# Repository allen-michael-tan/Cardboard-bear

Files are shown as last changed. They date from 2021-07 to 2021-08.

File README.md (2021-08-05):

# Cardboard bear

This repository showcases how a cardboard sculpture made by [Mr Bartholomew Ting](https://www.instagram.com/butterNmilk/) was modified and integrated with electronics to welcome students who step into Singapore Polytechnic's Makerspace. 

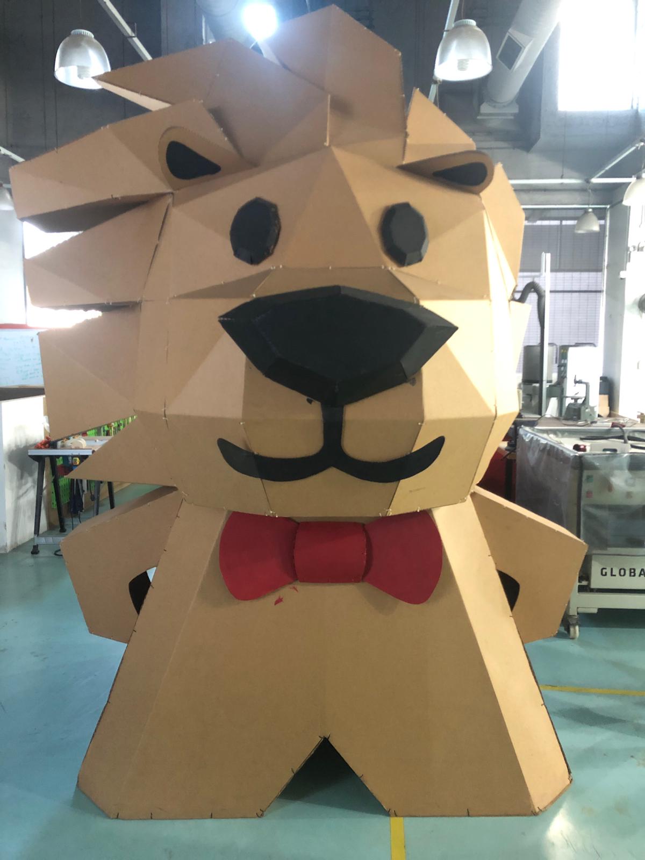
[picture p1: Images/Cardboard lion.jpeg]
Cardboard lion
 

This was how the original cardboard sculpture looked like. It was a lion, standing at a staggering height of over three meters! However, it was too tall to be placed in Makerspace which has a ceiling height of less than three meters. Therefore, modifications to the sculpture had to be made in order for it to be transported and placed in Makerspace.

Hence, the decision was made to remove the mane of the lion which happened to be enough height reduction for the sculpture to fit in Makerspace.

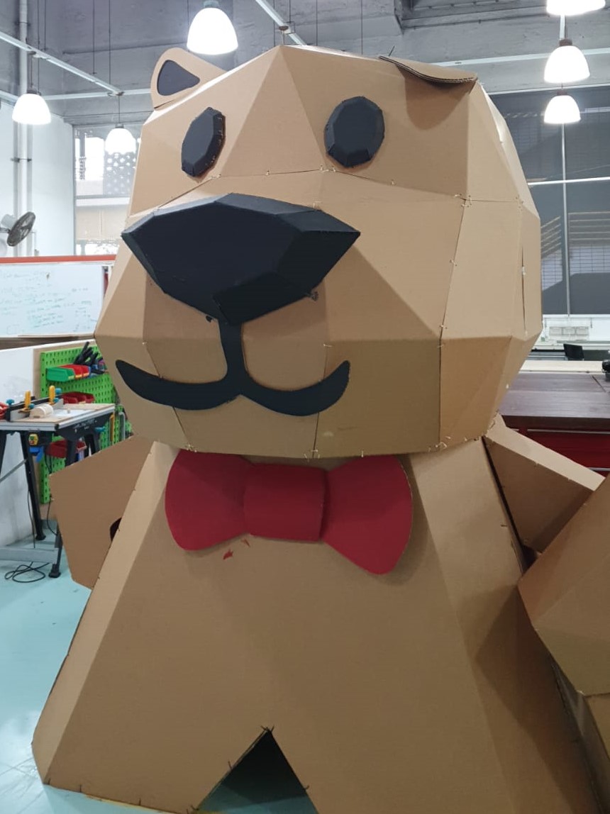
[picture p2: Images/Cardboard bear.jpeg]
Cardboard bear
 

This was how the cardboard sculpture after its "haircut". Without its mane, the lion looked very similar to a bear. Thus, the cardboard bear sculpture was born.

## Concept

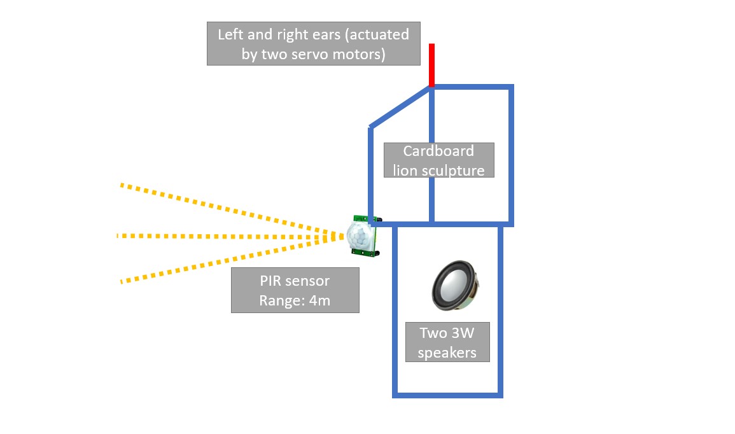
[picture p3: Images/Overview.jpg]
Overview


The concept of this project is when someone walks past the bear, it will be able to sense it through a sensor. After which, it will "interact" with the person by flapping its ear and playing a short audio track towards the person. 

Below is a short illustration of the concept.

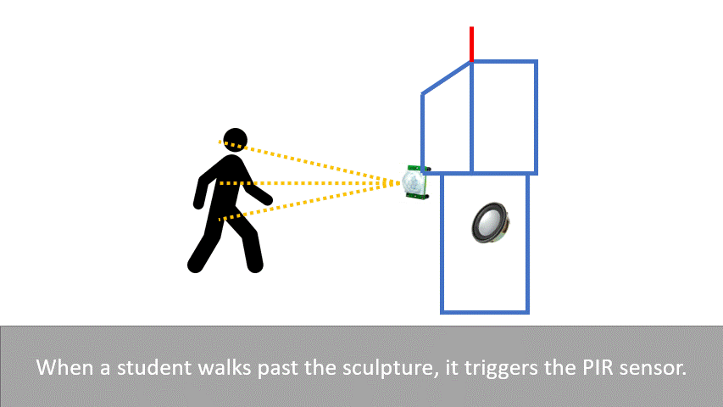
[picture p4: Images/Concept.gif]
Concept


## Design

All CAD models were modelled using Autodesk Inventor, the files can be found [here](https://github.com/allen-michael-tan/Kinematic-clock/tree/main/Inventor%20files).

The elctrical components used in this project are listed below. 

1. Arduino Uno [1]
2. SM-S3317B servo motors [2] 
2. PIR sensor [1]
3. DFR0299 MP3 player module [1] 
4. GF1002 amplifier module [1]
5. 3W speakers [2]
6. Button switch [1]
7. Blue LED bulb [1]
8. Red LED bulb [1]
9. 1k ohm resistor [3]

### Servo motor

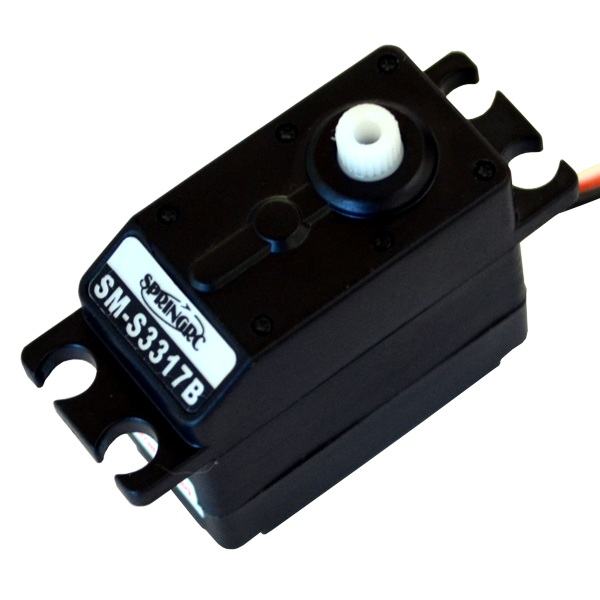
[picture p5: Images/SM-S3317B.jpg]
SM-S3317B


Both ears are individually actuated by servo motors. A mount for the servo motors were designed and 3D printed. 

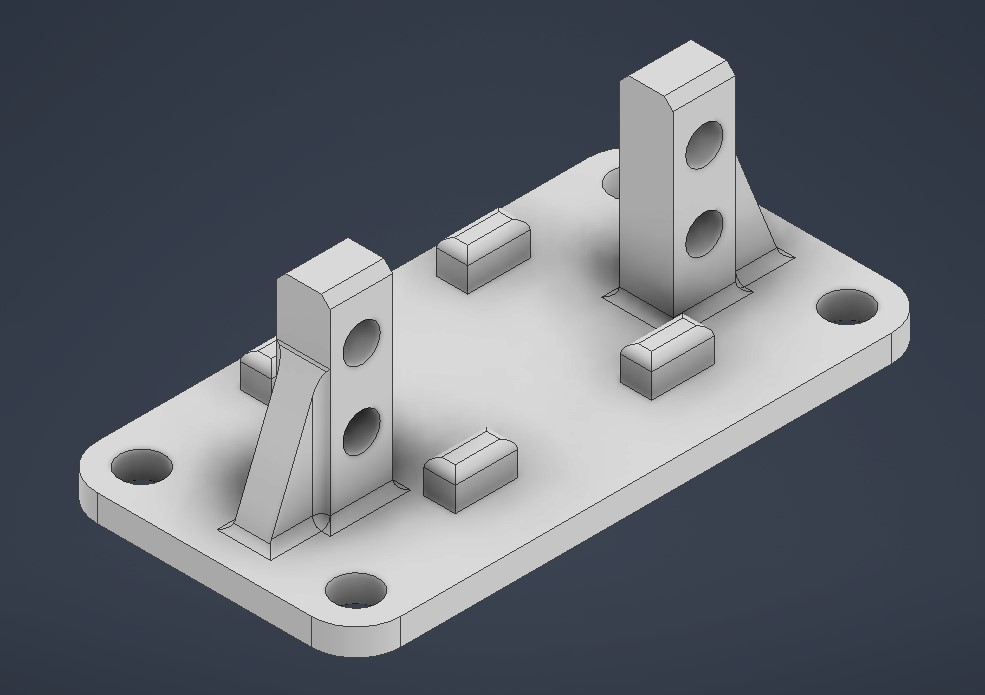
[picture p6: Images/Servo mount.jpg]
Servo mount


Two acrylic servo arms of 5mm thickness were laser cut, they were used in conjunction with nylon string to translate the motion of the servo motors to the ears.

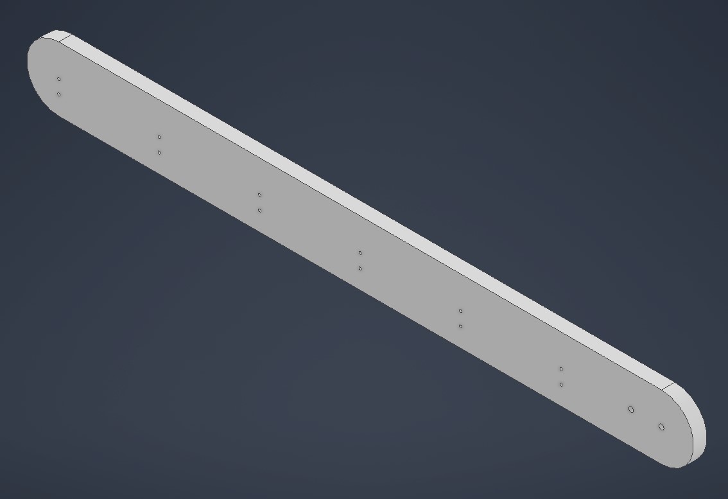
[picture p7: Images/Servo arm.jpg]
Servo arm


****

### PIR sensor

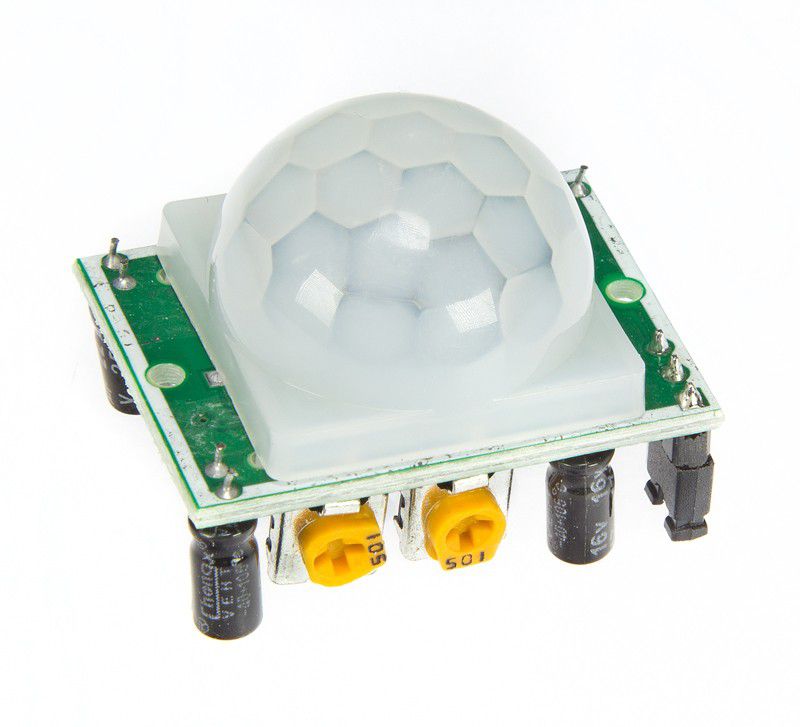
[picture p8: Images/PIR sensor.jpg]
PIR sensor


To attach the PIR sensor to the bottom of the "chin" of the bear, a 3D printed mount was made.

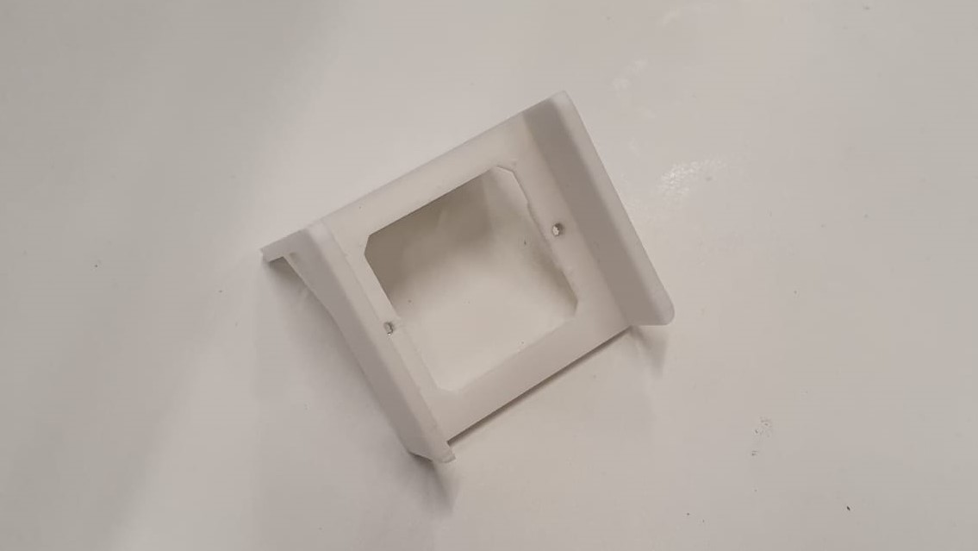
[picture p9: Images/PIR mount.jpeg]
PIR mount


****

### GF1002 Amplifier module

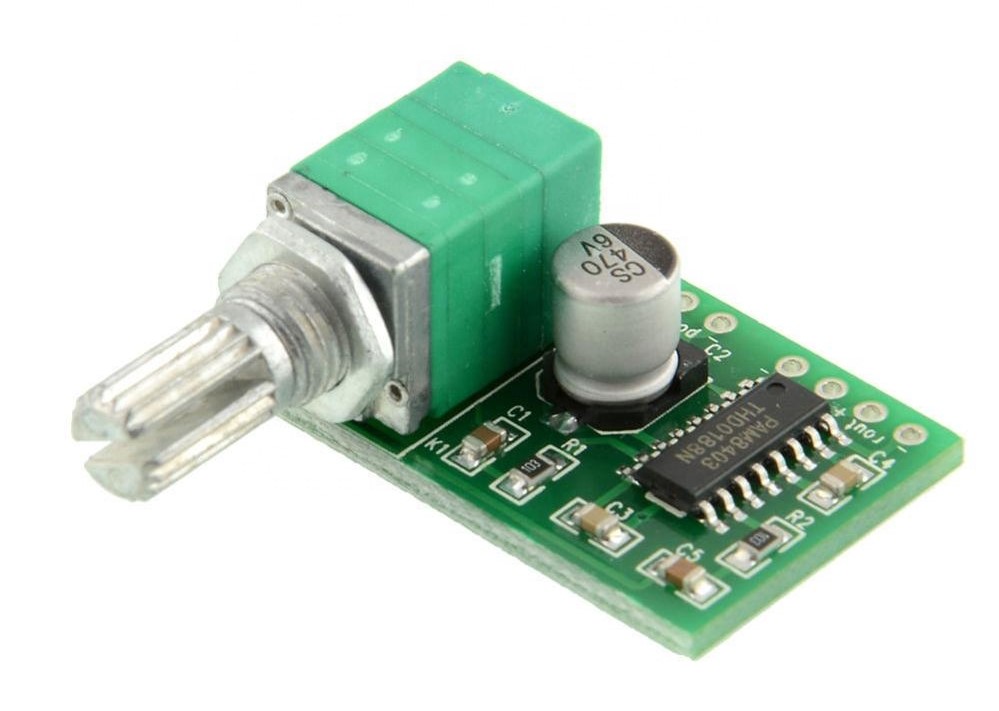
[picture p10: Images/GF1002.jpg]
GF1002


The purpose of this module is to allow users to easily control the volume of the speakers without the use of code. This module was installed inside the body of the bear. Thus, a 3D printed holder was made to ensure that it could be securely installed in the bear.

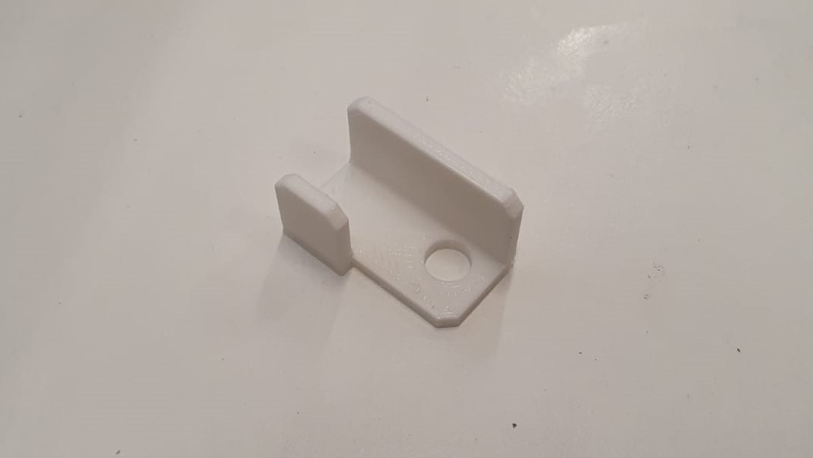
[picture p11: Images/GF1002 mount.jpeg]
GF1002 mount


To make it easier for users to adjust the volume of the speakers, a volume knob was designed and 3D printed. It was slotted into the potentiometer of the module. 

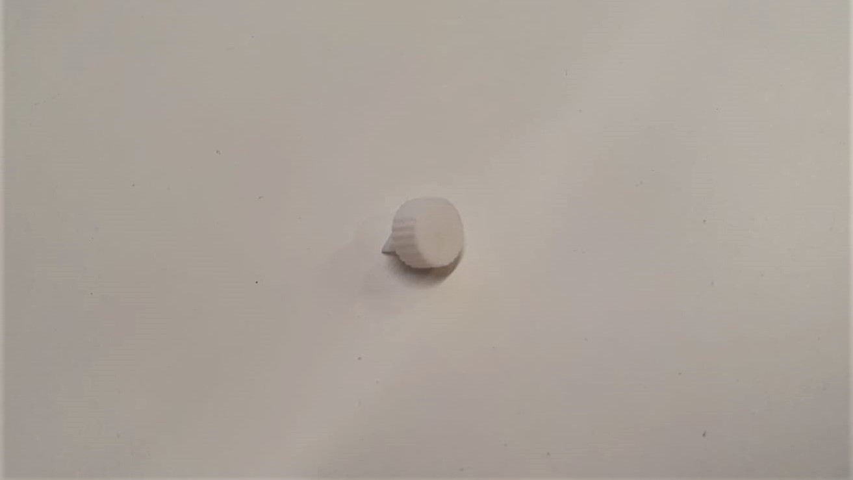
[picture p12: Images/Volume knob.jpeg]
Volume knob


****

### Interface board

An interface board is made to show what state the bear is in. Two different coloured LED bulbs - blue and red, were used to indicate the different states. To make it easy to install, a 3D printed cover with the relevant cutouts was made to cover the board. 

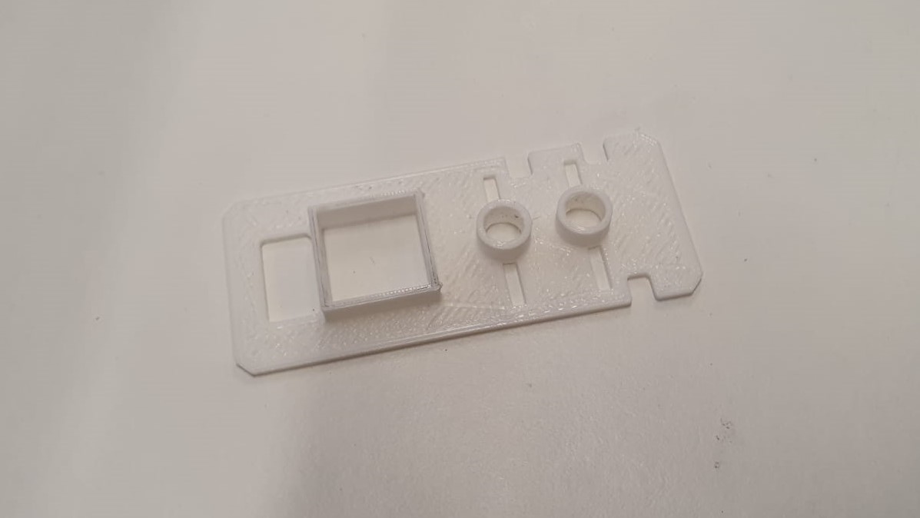
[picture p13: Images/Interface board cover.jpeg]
Interface board cover


## Electrical Wiring

Below is full schematic diagram of all components used.

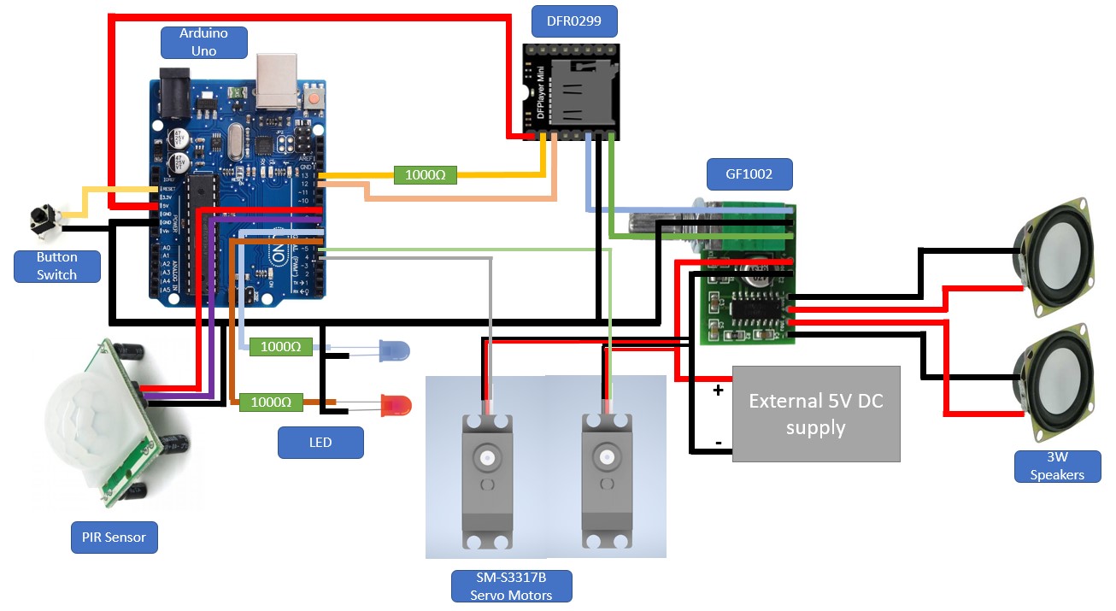
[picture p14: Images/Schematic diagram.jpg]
Schematic diagram


The amplifier module and servo motors will not draw power from the Arduino because the combined load of all components exceeded what the Arduino can output. Instead, they will draw power from an external source that outputs 5V DC.

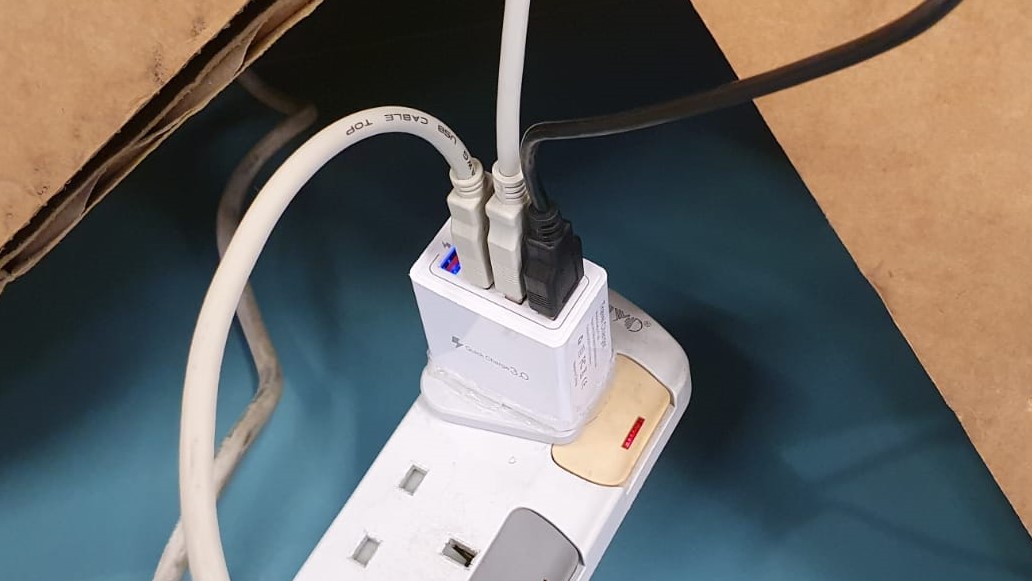
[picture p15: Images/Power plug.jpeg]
Power plug


A multi-USB phone charger wall plug was the choice of power delivery. It converts AC power to DC power and has enough current in each USB socket to power the Arduino, amplifier module, and the servo motors.  

### Circuit boards

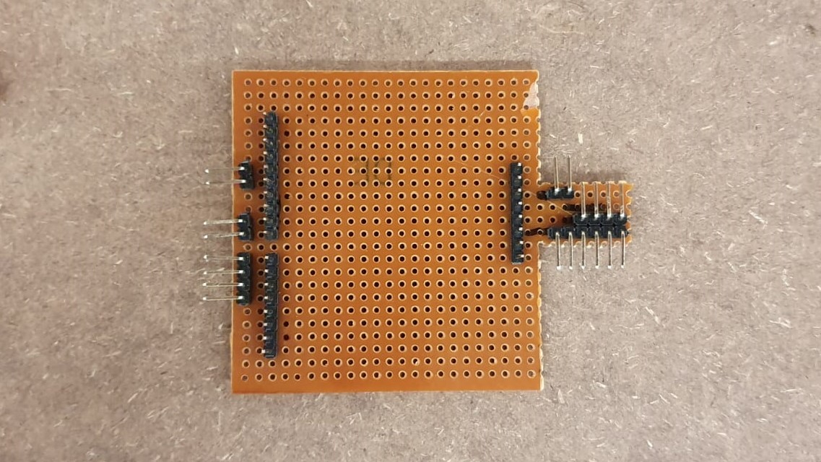
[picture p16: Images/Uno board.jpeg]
Uno board
 

*Arduino Uno expansion board*

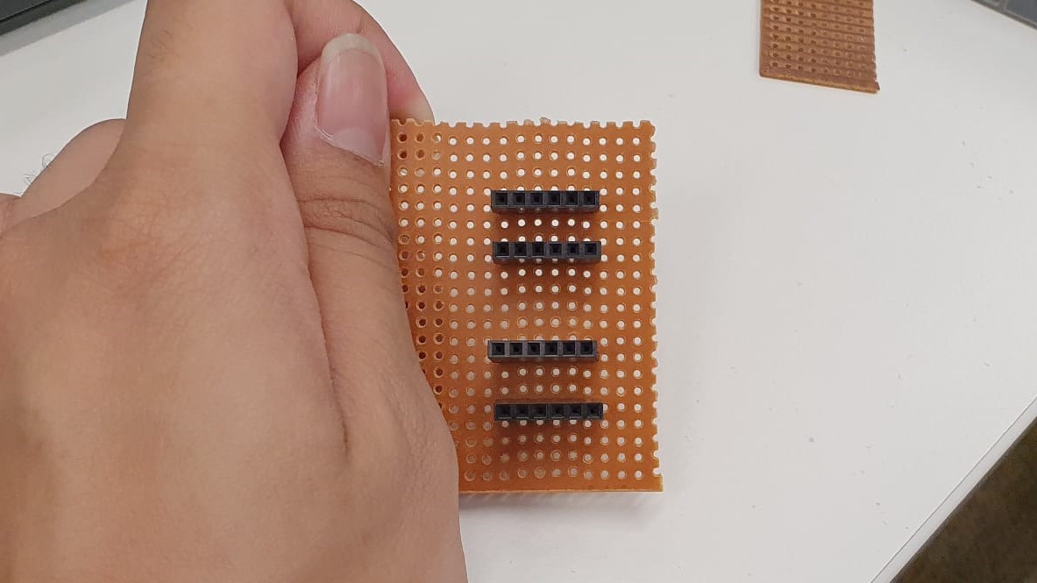
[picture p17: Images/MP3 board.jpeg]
MP3 board


*MP3 module expansion board* 

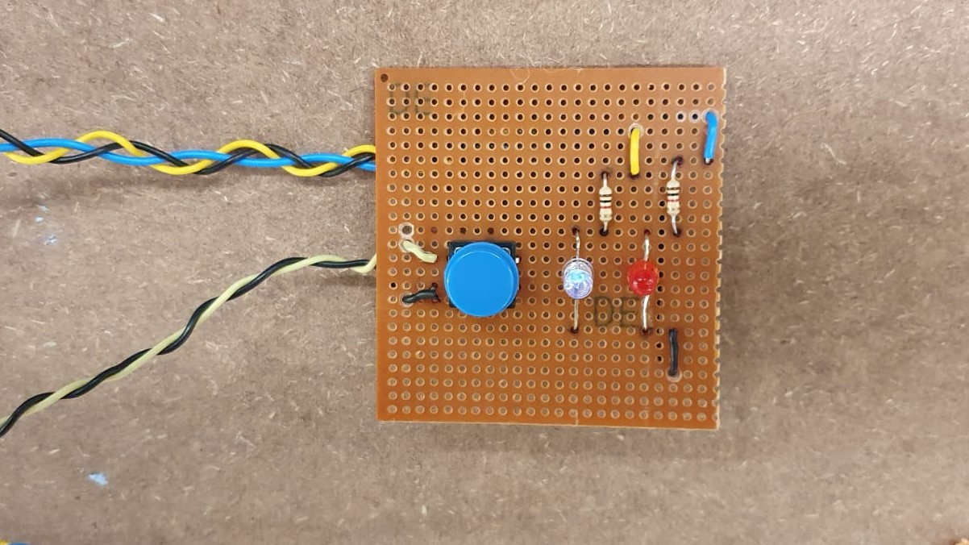
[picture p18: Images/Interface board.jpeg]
Interface board


The interface board consists of a button switch, red and blue LED bulbs. The switch is a reset switch for the entire circuit while the LEDs are indicating lights.

Extension cables of varying lengths were made, as for some components such as the servo motors require long wires (at least 2m) to be connected to the Arduino and power plug.

## Assembly

### Servo motors and ears

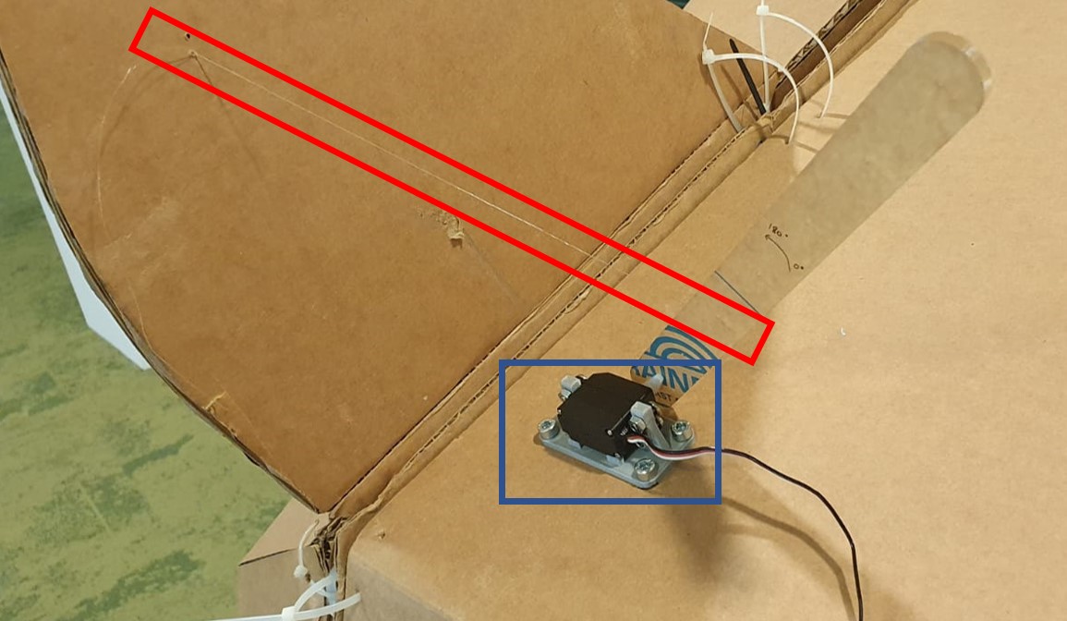
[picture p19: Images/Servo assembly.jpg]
Servo assembly


As shown was the assembly of the ear movement system. The servo motor (blue box) was bolted onto the servo mount with bolts and nuts. Next, holes were drilled into the top of the head so that the mount could be bolted down. At the same time, the acrylic servo arm was also securely attached to the servo motor with screws. Lastly, nylon thread [red box] was used to connect the servo arm to the ear through holes in the servo arm and holes that were pre-drilled into the ear.   

The process for the right ear was exactly the same. 

****

### GF1002 and speakers

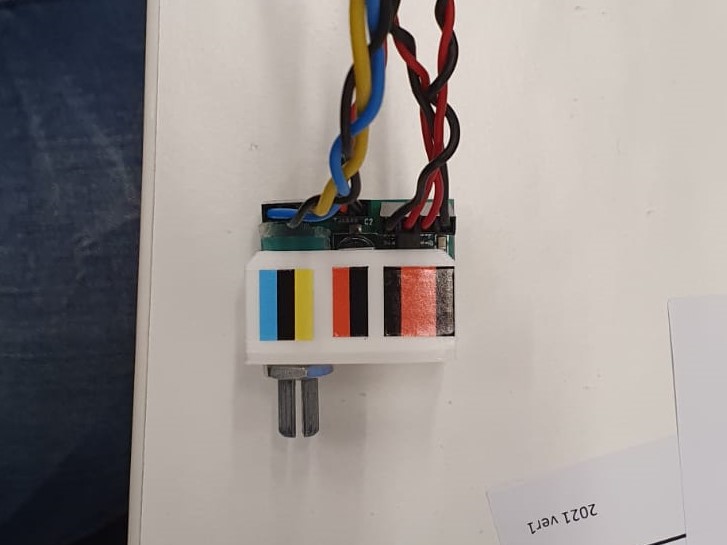
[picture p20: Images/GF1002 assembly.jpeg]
GF1002 assembly


This was how the amplifier module was installed onto its mount. 

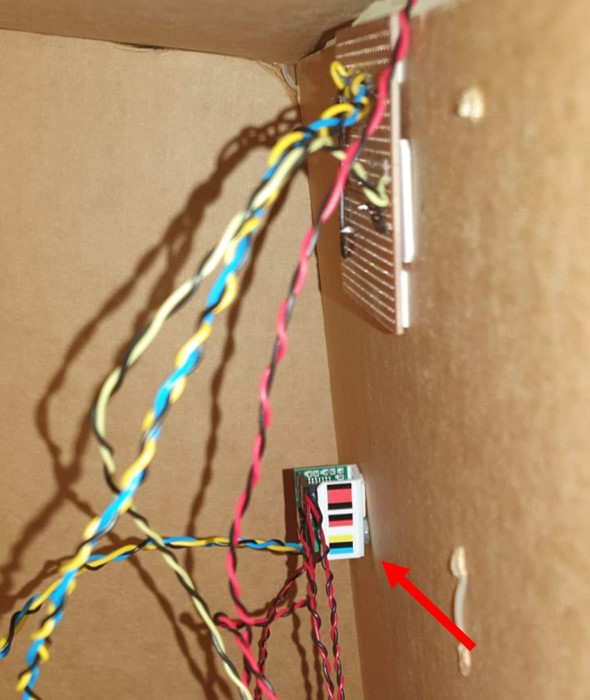
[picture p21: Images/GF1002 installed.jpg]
GF1002 installed


To attach the mount onto the body, double-sided foam tape was used (red arrow). A hole was pre-drilled to let the potentiometer protude out so that the volume knob can be pushed in from the front. 

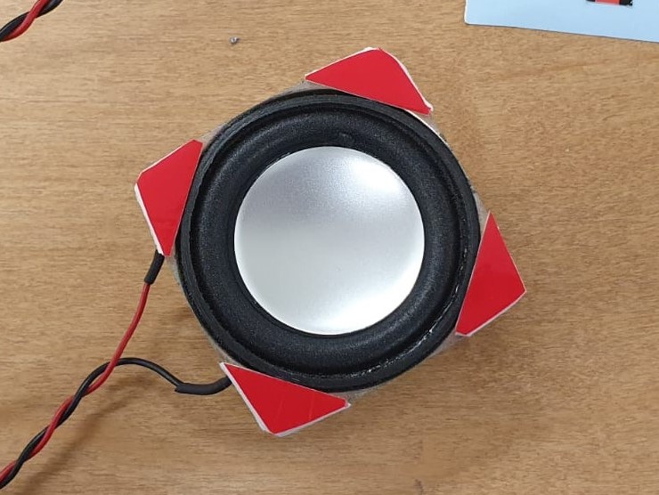
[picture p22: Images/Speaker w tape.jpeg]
Speaker w tape


The speakers were adhered onto the bear with the use of double-sided foam tape placed around the speaker as shown above. 

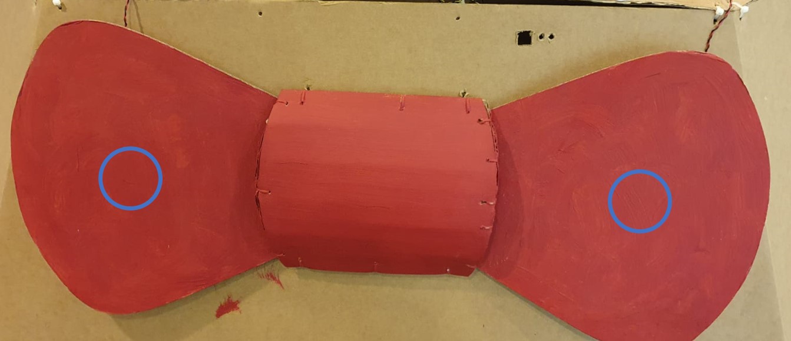
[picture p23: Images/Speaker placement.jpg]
Speaker placement


The speakers were attached behind the bow tie of the bear in the following circled locations.

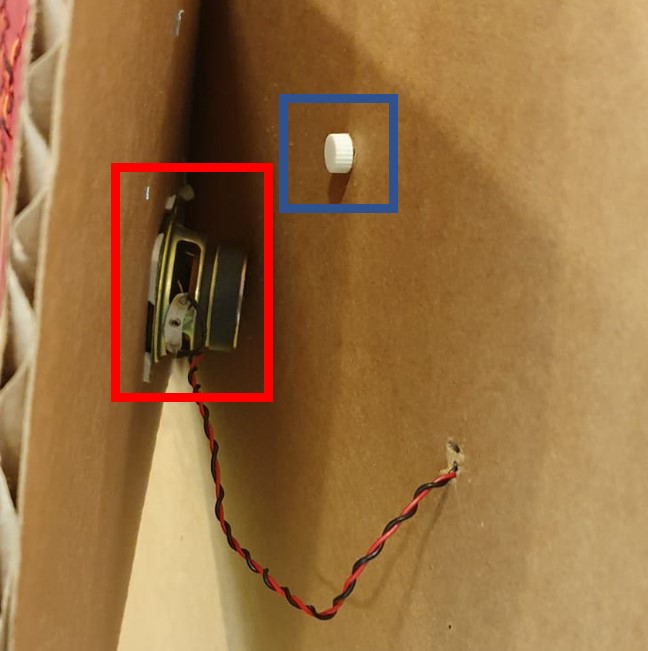
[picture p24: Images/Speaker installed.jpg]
Speaker installed
 

This was how the speaker (red box) looked like from behind the bow tie. 

Furthermore, the volume knob (blue box) was also pushed into the potentiometer. 

****

### Arduino Uno and MP3 module

To allow for easy access to the pins of the arduino, a hinged cut out was made to the top of the body of the bear. This way, in case any maintainence or troubleshooting had to be done, the head would only need to be tilted to make room for the cut out to be lifted up.

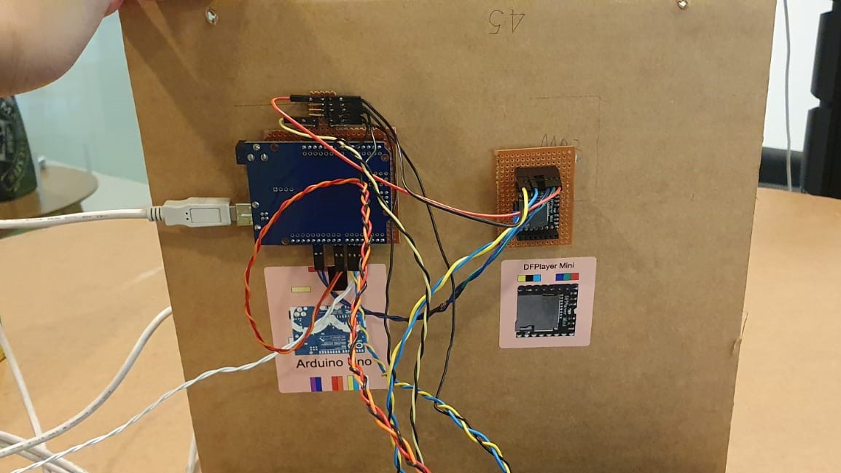
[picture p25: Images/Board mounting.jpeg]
Board mounting


The Arduino and MP3 expansion boards are adhered to the underside of the cut out using double-sided foam tape as shown above (Arduino and MP3 module had already been installed here). 

****

### PIR sensor

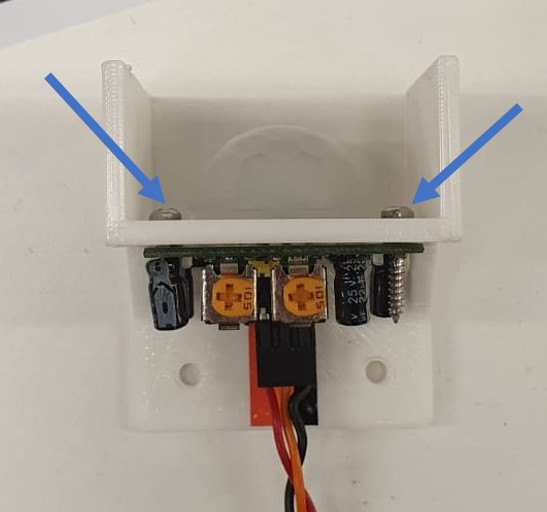
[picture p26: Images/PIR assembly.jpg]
PIR assembly


In the assembly of the PIR sensor to its mount, two screws (blue arrows) were used.

The PIR sensor was mounted on the underside of the bear's chin (blue box). However, velcro strips were used in place of bolts and nuts in the attachment of the sensor. This was because should the bear be transported elsewhere, it would be easier to pull the sensor away from the mount rather than to remove screws.

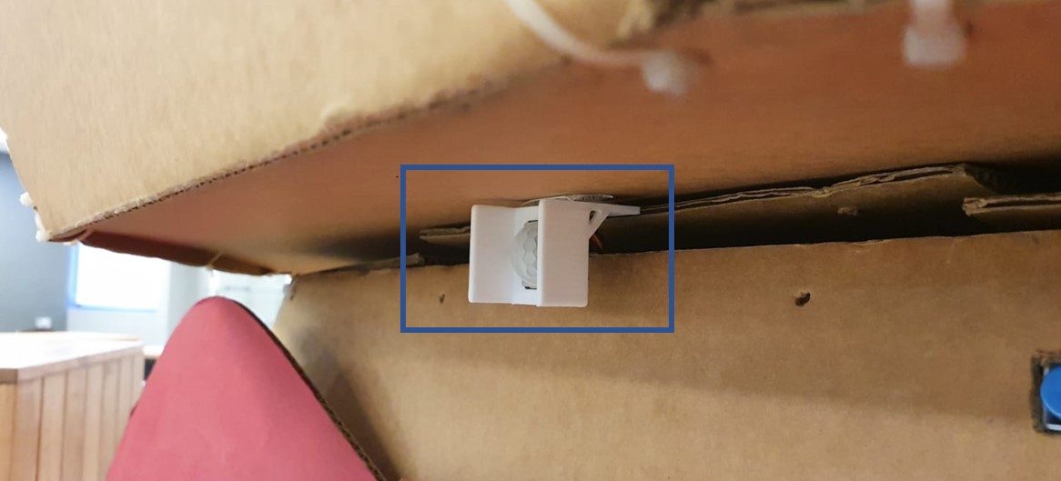
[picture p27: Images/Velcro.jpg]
Velcro


****

### Interface board

The interface board was covered with its 3D printed cover.

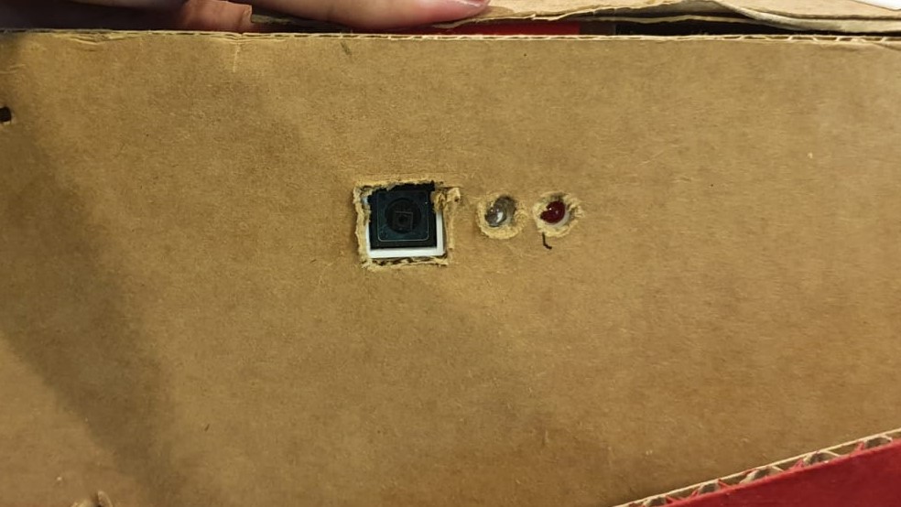
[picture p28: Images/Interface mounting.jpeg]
Interface mounting


To attach this board, two circular holes and a square hole above the bow tie were respectively drilled and cut out. Subsequently, the interface board with its covered was attached from the inside.  

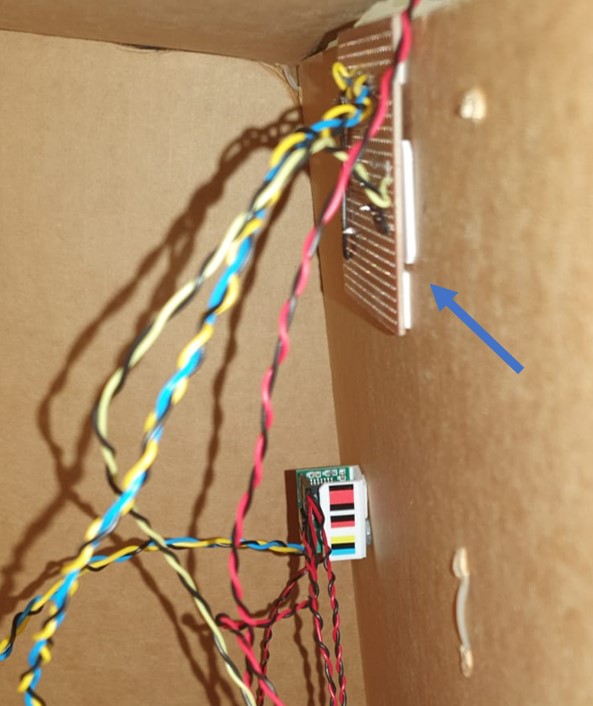
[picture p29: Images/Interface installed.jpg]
Interface installed


Double-sided foam tape was used to adhere the board (blue arrow) to the bear. 

****

### Putting them together

Before the head was placed on top of the body, all wires were connected to theirs corresponding ports except for the data wire of both servo motors. This was because those particular wires had to be connected to the GPIO pins of the Arduino which was situated in the body whereas the data wires were coming in from the head. 

Thus, as previously mentioned, a custom soldered wire was created, were the data wires were intertwined and made especially long. 

Steps taken to place the head onto the body:

1. After all other wires were connected, the head was lifted and placed on top of the body.
2. The data wires (encircled with yellow) of the servo motors were shoved into the gap between the head and face of the bear as shown below.
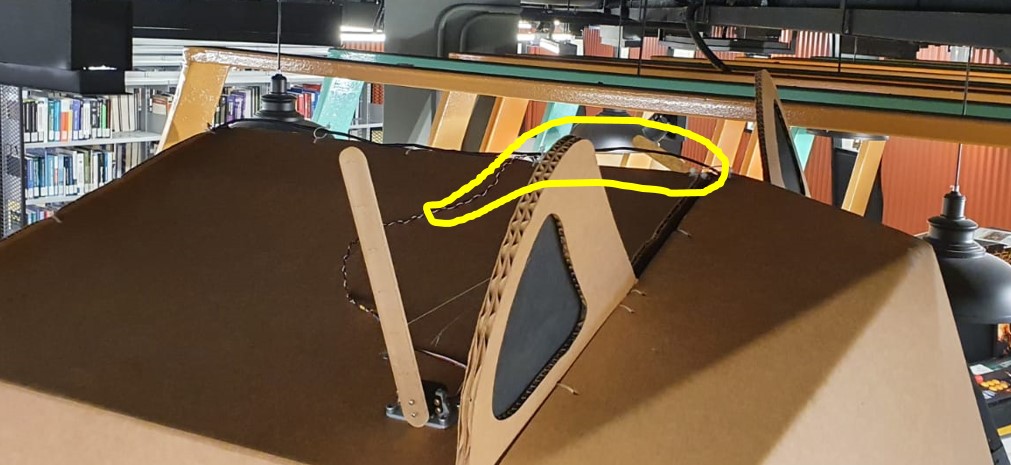
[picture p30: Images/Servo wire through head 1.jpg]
Servo wire through head 1

3. After that, the wires were routed through the gap to the bottom of the head. *(A white line was drawn on the image below for illustration.)*
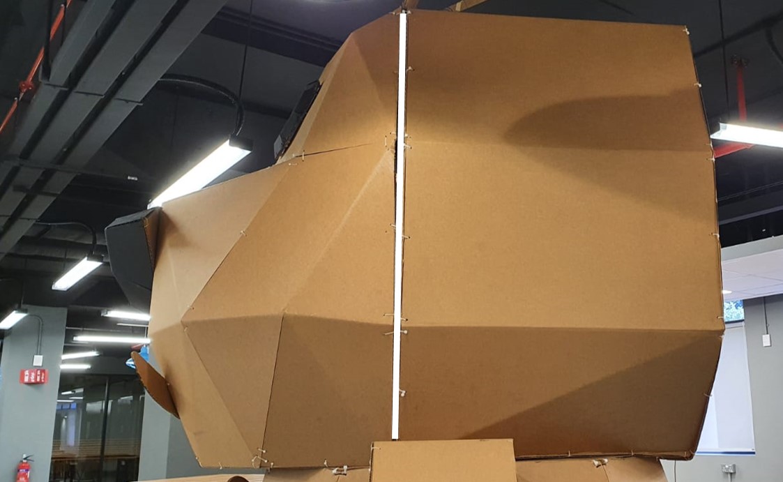
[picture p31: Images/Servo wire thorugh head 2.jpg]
Servo wire through head 2

4. Finally, the cut out in the body was lifted up, and the data wires were connected to the Arduino expansion board as shown (red box). *(Note, the shiny part of the dupont head should be face outside)
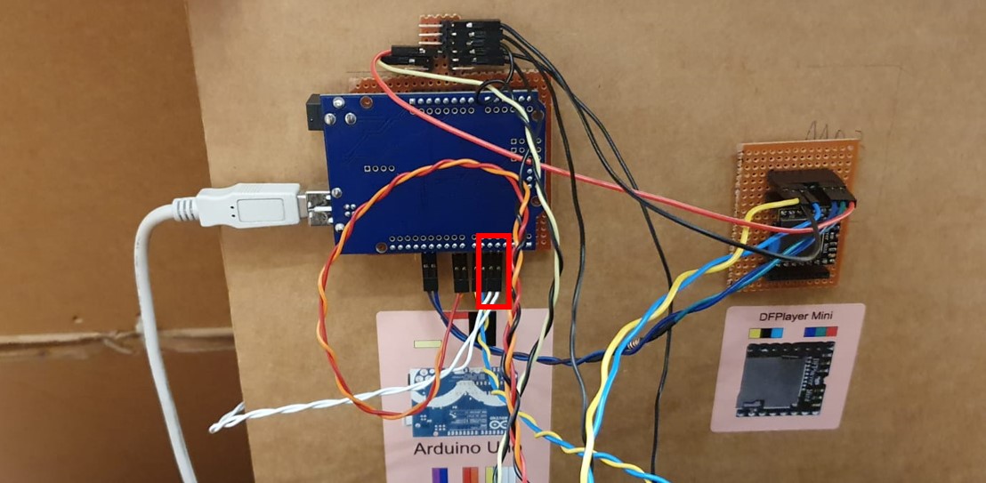
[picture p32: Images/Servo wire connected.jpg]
Servo wire connected
  

### Disassembly

For disassembly, there is a couple steps.

1. Disconnect the data pins of the servo motors from the Arduino expansion board and remove them from the body.
2. Detach the PIR sensor from the chin.
3. Remove the head from the body by carrying it away.

Now, the bear sculpture is in two pieces and can be transported safely and easily.

## Code 

All the codes used for the project can be found [here](https://github.com/allen-michael-tan/Cardboard-bear/tree/main/Code). 

### Servo motor code

	#include <Servo.h>
	
	Servo left;
	Servo right;
	
	int leftAngle = 20;
	int rightAngle = 25;
	
	void setup() {
	  left.attach(5);
	  right.attach(4);
	  left.write(20);
	  right.write(25);
	}
	
	void loop() {
	  for (rightAngle == 25; leftAngle < 90; leftAngle ++) {
	    left.write(leftAngle);
	    delay(7);
	  }
	  for (leftAngle == 90; rightAngle < 90; rightAngle ++){
	    right.write(rightAngle);
	    delay(7);    
	  }
	  for (rightAngle == 90; leftAngle > 20; leftAngle --) {
	    left.write(leftAngle);
	    delay(7);
	  }
	  for (leftAngle == 20; rightAngle > 25; rightAngle --) {
	    right.write(rightAngle);
	    delay(7);
	  }
	 }

### PIR sensor code

	int calibrationTime = 10; // Calibration time (10 - 60 secs)
	
	long unsigned int lowIn; // The time when the sensor outputs a low impulse
	long unsigned int pause = 5000; // The amount of milliseconds the sensor has to be low before assuming all motion has stopped
	
	boolean lockLow = true;
	boolean takeLowTime;
	
	int pirPin = 8; // Connects to PIR output pin
	int pirPos = 9; // Connects to PIR Vcc pin
	int LED = 7; // Connects to arduino pin 7
	
	void setup() {
	  Serial.begin(9600);
	  
	  pinMode(pirPin, INPUT);
	  pinMode(pirPos, OUTPUT);
	  digitalWrite(pirPos, HIGH);
	
	  Serial.println(); // Give sensor time to calibrate
	  Serial.println("Calibrating sensor "); 
	  for (int i = 0; i < calibrationTime; i++){
	    Serial.print(calibrationTime - i);
	    Serial.print("-");
	    delay(1000);
	  }
	  Serial.println();
	  Serial.println("Sensor calibration done!");
	
	  // To prevent the PIR's output from going HIGH immediately after calibrating, this while loop waits until the PIR's output is LOW before ending setup
	  while (digitalRead(pirPin) == HIGH) {
	    delay(500);
	    Serial.print(".");
	  }
	  Serial.print("SENSOR ACTIVE");
	}
	
	void loop() {
	  if(digitalRead(pirPin) == HIGH){ // If the PIR output is HIGH, LED will light up 
	
	    digitalWrite(LED, HIGH);
	 
	    if(lockLow){ // Makes sure the PIR waits for a transition to LOW before any further outputs are made
	      lockLow = false;
	      Serial.println("---");
	      Serial.print("Motion detected at ");
	      Serial.print(millis()/1000);
	      Serial.println(" sec");
	      delay(50);
	    }
	   takeLowTime = true;
	  }
	
	  if(digitalRead(pirPin) == LOW);{
	
	    digitalWrite(LED, LOW);
	
	    if(takeLowTime){
	      lowIn = millis(); // Saves the time of the transistion from HIGH to LOW
	      takeLowTime = false;
	    }
	
	    // If the sensor is LOW for more than the given pause, the PIR will assume all motion has stopped
	    if(!lockLow && millis() - lowIn > pause){ // Make sure this block of code is only executed again after a new motion sequence has been detected
	      lockLow = true;
	      Serial.print("Motion ended at "); // Output
	      Serial.print(millis() - pause/1000);
	      Serial.println(" sec");
	      delay(50);
	    }
	  }
	}

### MP3 module code

	#include <NeoSWSerial.h>
	#include "DFRobotDFPlayerMini.h"
	
	NeoSWSerial mp3(12,13);
	DFRobotDFPlayerMini myDFPlayer;
	
	void printDetail(uint8_t type, int value);
	
	void setup() {
	  Serial.begin(9600);
	  Serial.println("DFPlyaer with AltSoftSerial Test Begin");
	  mp3.begin(9600);
	  Serial.println("DFRobot DFPlayer Mini Demo");
	  Serial.println("Initializing Player ... (May take 3~5 seconds)");
	
	  if (!myDFPlayer.begin(mp3)) {
	    Serial.println("Unable to begin!");
	    Serial.println("1. Please recheck the connection!");
	    Serial.println("2. Please insert the SD card!");
	    Serial.println(myDFPlayer.readState());
	    Serial.println(myDFPlayer.readFileCounts());
	    while(true){
	      delay(0);
	    }
	  }
	  Serial.println("DFPlayer Mini online.");
	
	  myDFPlayer.volume(30); // Volume settings (from 0 - 30)
	}
	
	void loop() {
	  if (myDFPlayer.available()) {
	    printDetail(myDFPlayer.readType(), myDFPlayer.read()); // Print the detail message from DFPlayer to handle different errors and state.
	  }
	  myDFPlayer.randomAll(); // Randomly play all the tracks in the SD card
	}
	
	void printDetail(uint8_t type, int value){
	  switch (type) {
	    case TimeOut:
	      Serial.println(F("Time Out!"));
	      break;
	    case WrongStack:
	      Serial.println(F("Stack Wrong!"));
	      break;
	    case DFPlayerCardInserted:
	      Serial.println(F("Card Inserted!"));
	      break;
	    case DFPlayerCardRemoved:
	      Serial.println(F("Card Removed!"));
	      break;
	    case DFPlayerCardOnline:
	      Serial.println(F("Card Online!"));
	      break;
	    case DFPlayerUSBInserted:
	      Serial.println("USB Inserted!");
	      break;
	    case DFPlayerUSBRemoved:
	      Serial.println("USB Removed!");
	      break;
	    case DFPlayerPlayFinished:
	      Serial.print(F("Number:"));
	      Serial.print(value);
	      Serial.println(F(" Play Finished!"));
	      break;
	    case DFPlayerError:
	      Serial.print(F("DFPlayerError:"));
	      switch (value) {
	        case Busy:
	          Serial.println(F("Card not found"));
	          break;
	        case Sleeping:
	          Serial.println(F("Sleeping"));
	          break;
	        case SerialWrongStack:
	          Serial.println(F("Get Wrong Stack"));
	          break;
	        case CheckSumNotMatch:
	          Serial.println(F("Check Sum Not Match"));
	          break;
	        case FileIndexOut:
	          Serial.println(F("File Index Out of Bound"));
	          break;
	        case FileMismatch:
	          Serial.println(F("Cannot Find File"));
	          break;
	        case Advertise:
	          Serial.println(F("In Advertise"));
	          break;
	        default:
	          break;
	      }
	      break;
	    default:
	      break;
	  }
	}

Initially the <SoftwareSerial.h> library to control the MP3 module was used, however, that library conflicted with the <servo.h> library used to control the servos. It caused the servo motors to jitter and sometimes made them go spastic. Furthermore, the conflict also made the MP3 module unable to play any error.

Therefore, a solution to this was to use the <NeoSWSerial.h> library to control the MP3 module. 

Although there were other solutions such as using a servo motor driver to drive the servo motors or changeingto a different microcontroller such as an Arduino Mega that has hardware serial already built into the board. The <NeoSWSerial.h> library solution was ultimately chosen due to it being the easiest and lowest cost solution to implement.

### Full code

	#include <Servo.h>
	#include "Arduino.h"
	#include <NeoSWSerial.h>
	#include "DFRobotDFPlayerMini.h"  

	/*DFPlayer Mini definitions*/ 
	
	NeoSWSerial mp3(12,13); 
	DFRobotDFPlayerMini myDFPlayer;
	
	void printDetail(uint8_t type, int value);
	
	int mp3track;
	
	boolean audioPlay = true;
	
	/*Servo definitions*/
	
	Servo servo1;
	Servo servo2;
	
	// Starting positions of both servos (angle)
	int Angle1 = 20;
	int Angle2 = 25;
	
	/*PIR sensor definitions*/
	
	int calibrationTime = 10; // Calibration time (10 - 60 secs)
	
	long unsigned int lowIn; // The time when the sensor outputs a low impulse
	long unsigned int pause = 5000; // The amount of milliseconds the sensor has to be low before assuming all motion has stopped
	
	boolean lockLow = true;
	boolean takeLowTime;
	
	int pirPin = 8; // Connects to PIR output pin
	int pirPos = 9; // Connects to PIR Vcc pin
	int LEDB = 7; // Connects blue LED to arduino pin 7
	int LEDR = 6; // Connects red LED to arduino pin 6
	
	void setup() {
	  Serial.begin(9600);
	
	  digitalWrite(LEDR, HIGH);
	  delay(3000);
	  digitalWrite(LEDR, LOW);
	
	  /*DFPlayer Mini setup*/
	  
	  mp3.begin(9600);
	  Serial.println();
	  Serial.println(F("Initializing DFPlayer ... (May take 3~5 seconds)"));
	
	  if (!myDFPlayer.begin(mp3)) { // Use softwareSerial to communicate with mp3
	    Serial.println(F("Unable to begin:"));
	    Serial.println(F("1. Please recheck the connection!"));
	    Serial.println(F("2. Please insert the SD card!"));
	    Serial.println(myDFPlayer.readState()); // Read mp3 state
	    Serial.println(myDFPlayer.readFileCounts()); // Read all file counts in SD card
	    while (!myDFPlayer.begin(mp3)) { // Red LED will blink every 1s if mp3 player does not start
	      digitalWrite(LEDR, HIGH);
	      delay(1000);
	      digitalWrite(LEDR, LOW);
	    }
	  }
	  Serial.println(F("DFPlayer Mini online."));
	
	  myDFPlayer.volume(20); // Volume settings (from 0 - 30)
	  
	  /*PIR sensor setup*/
	
	  pinMode(pirPin, INPUT);
	  pinMode(pirPos, OUTPUT);
	  digitalWrite(pirPos, HIGH);
	
	  Serial.println(); // Give sensor time to calibrate
	  Serial.println("Calibrating sensor ");
	  for (int i = 0; i < calibrationTime; i++) {
	    Serial.print(calibrationTime - i);
	    Serial.print("-");
	    delay(1000);
	  }
	  Serial.println();
	  Serial.println("Sensor calibration done!");
	
	  // To prevent the PIR's output from going HIGH immediately after calibrating, this while loops waits until the PIR's output is LOW before ending setup
	  while (digitalRead(pirPin) == HIGH) {
	    delay(500);
	    Serial.print(".");
	  }
	  Serial.print("SENSOR ACTIVE");
	
	  /*Servo motors setup*/  
	
	  servo1.attach(5);
	  servo2.attach(4);
	  servo1.write(Angle1);
	  servo2.write(Angle2);
	
	  myDFPlayer.play(1); //Start up sound
	  digitalWrite(LEDB, HIGH); // Blue LED lights up for 5s when all setups are successful
	  delay(5000);
	  digitalWrite(LEDB, LOW);
	}
	
	void playaudio() { // Function for playing mp3
	  if (audioPlay) {
	    mp3track = random(1,23); // Play a random mp3 file in the sd card (from 1 to how many files there are)
	    myDFPlayer.play(mp3track);
	    audioPlay = false;
	  }
	  return;
	}
	
	void servocontrol() { // Function for controlling servos
	  if (digitalRead(pirPin) == HIGH) {
	    // servo1 will flap down first, then followed by servo2; after which servo1 will go back to its original position, then followed by servo2
	    for (Angle1 == 20; Angle1 < 90; Angle1 ++) {
	      servo1.write(Angle1);
	      delay(7); // Higher number = slower speed
	    }
	    for (Angle1 == 90; Angle2 < 90; Angle2 ++) {
	      servo2.write(Angle2);
	      delay(7);
	    }
	    for (Angle2 == 90; Angle1 > 20; Angle1 --) {
	      servo1.write(Angle1);
	      delay(7);
	    }
	    for (Angle1 == 20; Angle2 > 25; Angle2 --) {
	      servo2.write(Angle2);
	      delay(7);
	    }
	  }    
	  return;
	}
	
	void loop() {
	  if (myDFPlayer.available()) {
	    printDetail(myDFPlayer.readType(), myDFPlayer.read()); // Print the detail message from DFPlayer to handle different errors and state.
	  }
	
	  if(digitalRead(pirPin) == HIGH) { // If the PIR output is HIGH, control servo and play mp3
	
	    digitalWrite(LEDB, HIGH);
	    playaudio();
	    servocontrol();
	
	    if(lockLow) { // Makes sure the PIR waits for a transition to LOW before any further outputs are made
	      lockLow = false;
	      Serial.println("---");
	      Serial.print("Motion detected at ");
	      Serial.print(millis()/1000);
	      Serial.println(" sec");
	      delay(50);
	    }
	    takeLowTime = true;
	  }
	
	  if(digitalRead(pirPin) == LOW) {
	    digitalWrite(LEDB, LOW);
	    audioPlay = true;
	
	    if(takeLowTime) {
	      lowIn = millis(); // Saves the time of the transistion from HIGH to LOW
	      takeLowTime = false; // Make sure this is only done at the start of a LOW phase
	    }
	
	    // If the sensor is LOW for more than the given pause, the PIR will assume all motion has stopped
	    if(!lockLow && millis() - lowIn > pause) { // Make sure this block of code is only executed again after a new motion sequence has been detected
	      lockLow = true;
	      Serial.print("Motion ended at "); // Output
	      Serial.print((millis() - pause)/1000);
	      Serial.println(" sec");
	      delay(50);      
	    }
	  }
	}
	
	void printDetail(uint8_t type, int value) {
	  switch (type) {
	    case TimeOut:
	      Serial.println(F("Time Out!"));
	      break;
	    case WrongStack:
	      Serial.println(F("Stack Wrong!"));
	      break;
	    case DFPlayerCardInserted:
	      Serial.println(F("Card Inserted!"));
	      break;
	    case DFPlayerCardRemoved:
	      Serial.println(F("Card Removed!"));
	      break;
	    case DFPlayerCardOnline:
	      Serial.println(F("Card Online!"));
	      break;
	    case DFPlayerUSBInserted:
	      Serial.println("USB Inserted!");
	      break;
	    case DFPlayerUSBRemoved:
	      Serial.println("USB Removed!");
	      break;
	    case DFPlayerPlayFinished:
	      Serial.print(F("Number:"));
	      Serial.print(value);
	      Serial.println(F(" Play Finished!"));
	      break;
	    case DFPlayerError:
	      Serial.print(F("DFPlayerError:"));
	      switch (value) {
	        case Busy:
	          Serial.println(F("Card not found"));
	          break;
	        case Sleeping:
	          Serial.println(F("Sleeping"));
	          break;
	        case SerialWrongStack:
	          Serial.println(F("Get Wrong Stack"));
	          break;
	        case CheckSumNotMatch:
	          Serial.println(F("Check Sum Not Match"));
	          break;
	        case FileIndexOut:
	          Serial.println(F("File Index Out of Bound"));
	          break;
	        case FileMismatch:
	          Serial.println(F("Cannot Find File"));
	          break;
	        case Advertise:
	          Serial.println(F("In Advertise"));
	          break;
	        default:
	          break;
	      }
	      break;
	    default:
	      break;
	  } 
	}

As mentioned before, apart of being used to reset the entire circuit, the other function of the interface board is to indicate the different state at which the bear is at. There are four states.

- **First state: System start up**

When the bear is first powered on, the red LED light up for 3 seconds.

- **Second state: MP3 startup failure**

If the MP3 failed to start, the red LED will blink every 1 second.

- **Third state: Successful start up**

Upon a successful system start up, the blue LED will light up for 5 seconds. In addition to that, the speakers will play a welcome message to indicate the bear is working.

- **Fourth state: Motion detected**

When the PIR sensor detects any motion i.e. a student walking past, the blue LED will turn on as long as there is any motion detected until all motion has ended five seconds after the last detected motion. 

## Operation

**Start up problem**

There is this problem where the speakers will produce satic noise immediately after the bear was powered on. To find out more about this problem, the link is below.

Problem video (https://youtu.be/13f0RLJsI6g)

The solution is to mute the speakers first by turning the volume knob anticlockwise until a click sound could be heard. Next, turn the bear off but switching off the plug, wait for the plug to power down completely before switching it on again. Unmute and turn up the volume of the speakers and wait. If the static noise still persists, let the speakers play for awhile. If that does not work, repeat the aforementioned process. To find out more, a video is shown below.

Solution video (https://youtu.be/AegnCoVfNu4)

**Adding/removing sound tracks**

To add or remove sound tracks, the steps are as follows:

1. Remove the micro SD card from the MP3 module.
2. Open the mp3 folder in the SD card.
3. Add or remove sound tracks in the folder, follow the naming convention as the other tracks in the folder.
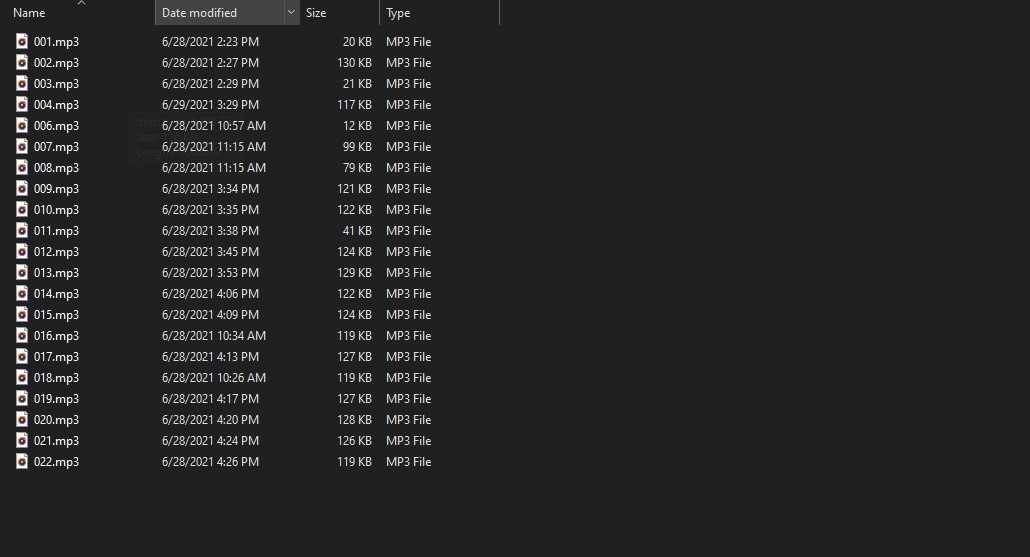
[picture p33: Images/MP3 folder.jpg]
MP3 folder
 **Note: It is very important to not remove or change the sound track named "001" and keep the sound track within 5 seconds and the format is in ".mp3".**
4. Insert the SD card back to the MP3 module.
5. For this line of code - " mp3track = random(1,23);" change the number "23" to the number of the last sound track. For example if the final sound track is named "031.mp3", change "23" to "31". 
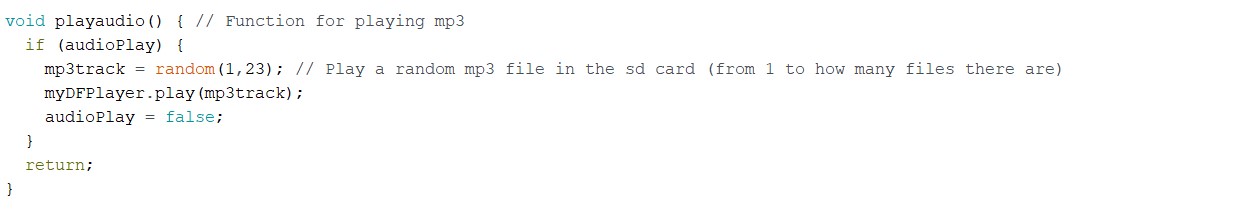
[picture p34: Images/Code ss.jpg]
Code ss


## Final Product

Below are an image of the finished cardboard bear project and a short video of the bear in operation.

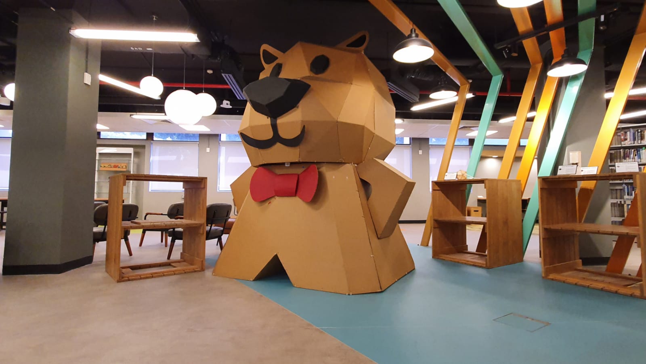
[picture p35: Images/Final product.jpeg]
Final product


*Finished project*

Product video (https://youtu.be/WaNZcLU6RV4)

*Short video of the bear in action*

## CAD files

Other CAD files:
Inventor files/GF1002 mount.ipt
Inventor files/Interface board cover.ipt
Inventor files/Motor arm.ipt
Inventor files/Motor mount.ipt
Inventor files/PIR mount.ipt
Inventor files/Volume knob.ipt
